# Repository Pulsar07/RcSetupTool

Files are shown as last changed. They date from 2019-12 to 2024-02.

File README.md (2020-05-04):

<div class="PageDoc">

<div class="header">

<div class="headertitle">

<div class="title">

RC-Einstell-Tool Projekt zur Ansteuerung eines Modellflug-Servos und zum
Vermessen von Ruderausschlägen mittels eines Winkelsensors

</div>

</div>

</div>

<div class="contents">

<div class="textblock">

# <span id="intro_sec_de" class="anchor"></span> Übersicht

Das RC Einstell Tool kann eine Servo mittels PWM Pulserzeugung steuern
und die Ansteuerdaten anzeigen. Zusatzlich kann mittels eines
Winkelsensors der Ruderausschlag sehr genau vermessen werden (besser als
0.5mm). Die Benutzeroberfläches ist als Web-Oberfläche ausgelegt, was
eine Bedienung auch mit dem Smartphone zulässt. Eine einfach kleine
Power-Bank dient als Stromversorgung und man kann extrem einfach und
schnell auf der Werkbank beim Bau oder bei Endeinstellarbeiten alle
wichtigen Daten schnell, genau und vollkommen reproduzierbar ablesen.
Hiermit lassen sich Einstellarbeiten auf der Werkbank oder am
aufgebauten Modell sehr professionell, schnell, genau und reproduzierbar
durchführen. Dieses Projekt ist die Zusammenführung von
<https://github.com/Pulsar07/RuderwegMessSensor> und
<https://github.com/Pulsar07/ServoController>
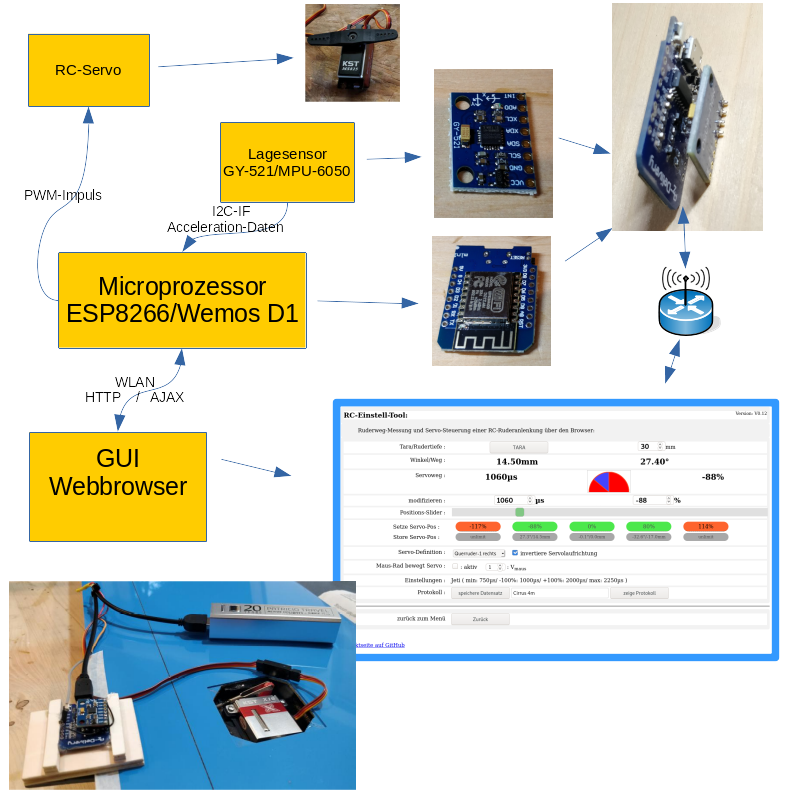
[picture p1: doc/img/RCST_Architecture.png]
Architektur


# <span id="hardware_sec_de" class="anchor"></span> Hardware

## <span id="hardware_subsec_de_mk" class="anchor"></span> Mikrokontroller

Als Mikrokontroller wird der Wemos D1/ESP8266 benutzt, der ausreichende
Rechenpower und Speicherresourcen bietet und eine WLAN Schnittstelle
hat. Es stehen ausgereifte Bibliotheken zur Nutzung der WiFi
Schnittstelle, zur Bereitstellung eines Web-Servers (GUI) und auch zur
Ansteuerung von Servos zur Verfügung.

Hier ein paar Links:

  - <https://www.az-delivery.de/products/d1-mini>
  - <https://github.com/esp8266/Arduino>

## <span id="hardware_subsec_de_ms" class="anchor"></span> Messsensor

Als Messsensor wird der GY-521/MPU-6050 benutzt. Die Genauigkeit liegt
nach Kalibrierung bei Winkeln bis +/- 45° kleiner als 0.5°. Der Baustein
MPU-6050 wird von einer wirklich sehr gut gemachten Libs von J.Rowberg
unterstützt (siehe Link) Der Aufbau sollte auch ohne den Winkelsensor
funktionieren, um nur die Funktion des Servo-Controllers zu erhalten.

Hier ein paar Links:

  - <https://www.invensense.com/wp-content/uploads/2015/02/MPU-6000-Datasheet1.pdf>
  - <https://www.az-delivery.de/products/gy-521-6-achsen-gyroskop-und-beschleunigungssensor>
  - <https://github.com/jrowberg/i2cdevlib/tree/master/Arduino/MPU6050>

## <span id="hardware_subsec_de_sc" class="anchor"></span> Servo-Controller

Für den Servo-Controller ist außer dem Signal-Kabel vom D7-Pin des
Microcontrollers keinerlei Hardware notwendig. Will man nur einen
Winkelmesser bauen, kann dieses Kabel einfach weggelassen werden.

## <span id="hardware_subsec_de_sp" class="anchor"></span> Schaltplan

Der Schaltplan ist denkbar einfach. Es werden nur 4 Verbindungen
zwischen Sensorplatine und Mikrokontroller benötigt. Das Layout und die
Software sind so ausgelegt, dass mit einer Stiftleiste 4x1 das
Sensorboard mit dem Gesicht in Richtung Mikrokontroller direkt verlötet
werden kann.
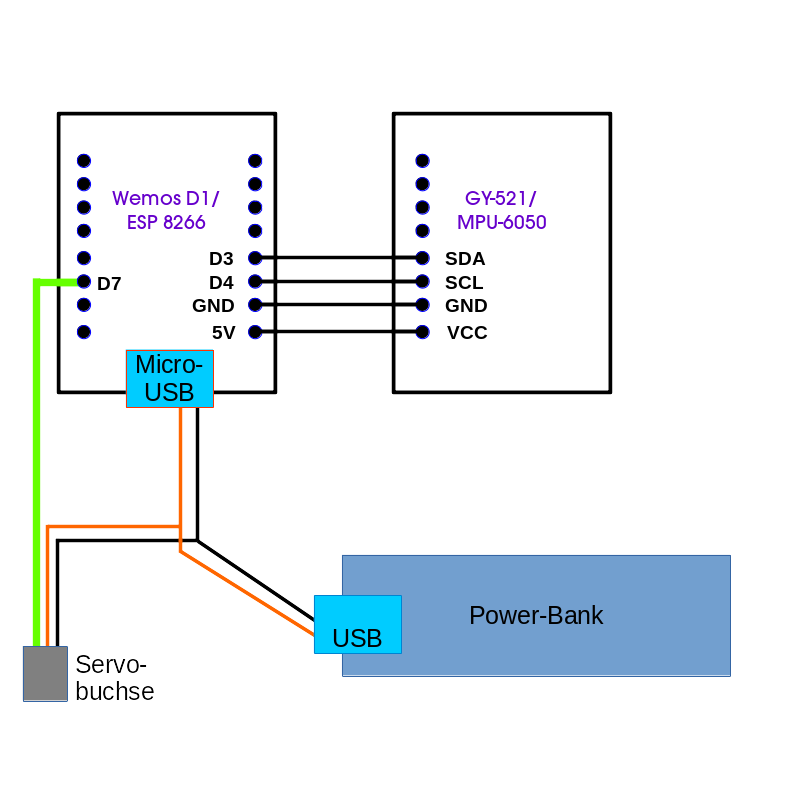
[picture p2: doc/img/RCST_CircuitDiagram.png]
Schaltplan
  
Der Servo wird lediglich mittels eines Signal-Kabels auf den D7 Pin des
Microcontrollers verbunden. Die Plus- und Ground-Verbindung wird mittels
eines auftrennten und wieder zusammengefügten USB-MicroUSB Kabels
hergestellt. Die Servo Stromversorgung wird einfach mittels eines
Servo-Buchsenkabels erstellt und sollte nicht über den Microkontroller
erfolgen, da die Stromstärke zu hoch für diesen ist.

## <span id="hardware_subsec_de_kv" class="anchor"></span> Ruderklemmvorrichtung

Hier kann der geneigte Modellbauer die Kombination aus Microprozessor
und Sensor in eine geeignete Klemmvorrichtung \[ein-\]bauen, die ein
rutschfestes Klemmen am Ruder gewährleistet. So sieht der Prototyp des
Authors aus:
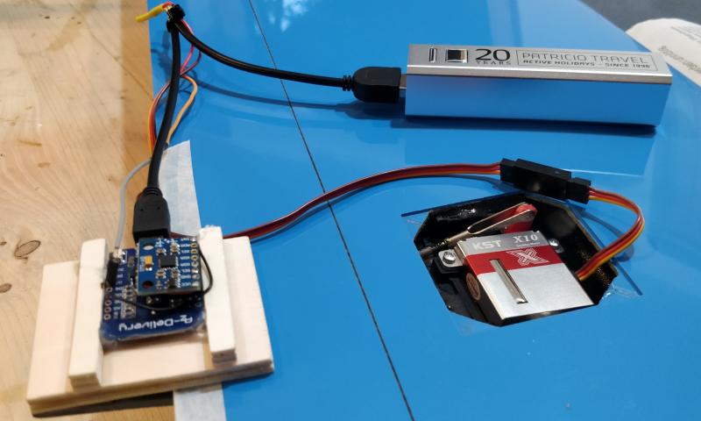
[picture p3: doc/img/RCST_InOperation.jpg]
Klemm


# <span id="hmi_sec_de" class="anchor"></span> Anleitung

## <span id="hmi_subsec_de_ib" class="anchor"></span> Inbetriebnahme

  - Stromversorgung
      - Der Sensor / das Mikroprozessorboard ist mit einem
        Micro-USB-Anschluss ausgestattet, hier kann man jedes
        handelsübliche USB-Netzteil anschließen oder besser jede
        normale Powerbank. Damit ist man in der Werkstatt oder auf dem
        Flugfeld mobil ausgestattet.
  - WiFi
      - Der Sensor muss zuerst mit Smartphone oder PC verbunden werden.
        Dazu stellt der Sensor per WiFi einen Accesspoint mit der SSID
        "UHU" und Kennwort "12345678" zur Verfügung. Ist das Gerät mit
        diesem WLAN verbunden, kann im Web-Browser über die Adresse
        <http://192.168.4.1> die Benutzeroberfläche benutzt und der
        Sensor konfiguriert werden. Sowohl obige SSID als auch das
        Kennwort können danach geändert werden.
      - Auf der Einstellseite kann eine SSID und ein Kennwort für ein
        WLAN (WLAN-Client) konfiguriert werden, mit dem sich der Sensor
        verbinden. Dabei wird dem Sensor eine IP-Adresse zugewiesen, die
        am WLAN-Router abgefragt werden muss. Änderungen der WLAN
        Einstellungen müssen gespeichert werden und werden erst nach
        Neustart aktiv.
      - Ist die Verbindung zu einem WLAN konfiguriert (WLAN-Client),
        kann auf der Einstellungsseite, der Accesspoint deaktiviert
        werden (nach Speichern und Neustart). Kann beim Neustart keine
        Verbindung zum konfigurierten WLAN aufgebaut werden, wird der
        Accesspoint-Mode aber trotzdem aktiviert, damit ein Zugang zum
        Gerät möglich ist.
  - Nutzung des Sensorboard GY-521 mit MPU-6050
      - Genauigkeit: Der MEMS Chip des MPU-6050 sollte Winkelauflösungen
        besser als 0.5° bei 45° Ausschlag messen können, was bei einer
        60mm Rudertiefe von 60mm einen Fehler von kleiner als 0.5mm
        ergibt. Zudem sind diverse Anzeigegenauigkeiten für die Winkel
        und die Ruderwegs-Messung auswählbar. Die Anzeige hat zwar immer
        2 Dezimalstellen, intern wird aber gerundet.
      - Experten-Einstellungen:
          - Kalibrierung: Damit der MPU-6050 allerdings diese
            Genauigkeit erreicht, muss er nachträglich kalibriert
            werden. Die Software unterstützt diese Funktion und kann die
            Werte intern speichern. Zur Kalibrierung muss die
            GY-521-Sensorplatine mit der flachen Rückseite möglichst
            exakt horizontal aufgelegt werden. Dann den Kalibrier-Button
            drücken und ca. 5s warten bis die Kalibrierung beendet ist.
            Dabei sollte die Auflagefläche (Tisch) nicht bewegt werden
            und frei von Vibrationen sein.
          - Einbaulage: Die Sensorplatine sollte auch genau so, wie bei
            der Kalibrierung, betrieben werden. Also die flache Seite
            nach unten und die Seite mit den Elektronikbausteinen nach
            oben. Nur so wird die oben genannte Genauigkeit erreicht.
          - Achsen und Anzeige-Genauigkeit: Auf der Konfigurationsseite,
            kann die Bezugs-Achse der Winkelmessung, je nach Einbaulage
            in der Klemmeinrichtung ausgewählt werden.
          - Kalibrierungsoffset: Hier können Kalibrierungs-Messwerte für
            +/- 45° Referenzmessungen eingebeben werden und
            aktiviert/deaktiviert werden, um die höchst mögliche
            Genauigkeit zu erreichen. Damit werden dann die Messwerte
            auf die Offsetwerte interpoliert. Der Grund hierfür ist, wie
            die Erfahrung zeigt, dass die verfügbaren günstggen
            China-Importe, nicht die höchste Qualität aufweisen. Z.T.
            lassen sich diese Sensoren einfach nicht kalibrieren. Ein
            manuelles Kalibrieren mit diesem Kalibrierungsoffset, bringt
            jedoch meist den gewünschten Erfolg (siehe
            Experten-Einstellungen) und gewährleistet genaues Arbeiten.

## <span id="hmi_subsec_de_me" class="anchor"></span> Winkel-Messung

  - Der mit dem Mikrokontroller verbundene Messensor sollte mit einer
    Klemmvorrichtung fest verbunden sein, und kann dann einfach an eine
    beliebige Stelle des Ruders aufgeklemmt werden. Die Ruderdrehachse,
    sollte möglichst parallel zur ausgewählten Dreh-Achse (X- oder
    Y-Achse) sein. Wie schon beschrieben, muss der Sensor mit dem
    Gesicht nach oben auf dem Ruder befestigt sein.
  - Einschränkungen: Der Sensor kann nur Winkel in Bezug auf die
    Schwerkraft messen. Somit sind Ruderwegsmessungen für das
    Seitenruder nur möglich wenn der Rumpf um 90° gedreht liegt.
  - Der Ruderweg ist abhänig von der Rudertiefe. Diese ist an der Stelle
    zu Messen, an der man den Ruderweg messen will. In der
    Web-Oberfläche des Sensor kann diese Rudertiefe eingegeben werden.
  - Ist der Sensor so auf dem Ruder angebracht, und die Rudertiefe
    eingestellt, ist die Ruderstellung in die Null-Lage zu bringen.
    Jetzt können Winkel und Ruderweg per "Tara"-Button auf 0 gesetzt
    werden.
  - Bewegt man das Ruder nun nach oben oder unten werden die Ausschläge
    in Grad und Millimeter angezeigt. Sollte das Vorzeichen nicht den
    Erwartungen entsprechen, kann dies bei den Einstellungen angepasst
    werden.
  - Zur Flugphasenmessung kann die Min-/Max-Rudermessung benutzt werden.
    Hier sollte man das Ruder in die Neutralstellung der Flugphase
    bringen. Nun den Schalter für die Min-/Max-Ruderweg-Messung
    aktivieren. Damit wird der aktuelle Ruderausschlag als Neutralwert
    übernommen. Jetzt können die beiden Min-/Max-Werte angefahren
    werden. Alle drei Werte werden bis zur Deaktiverung der Messung
    angezeigt.
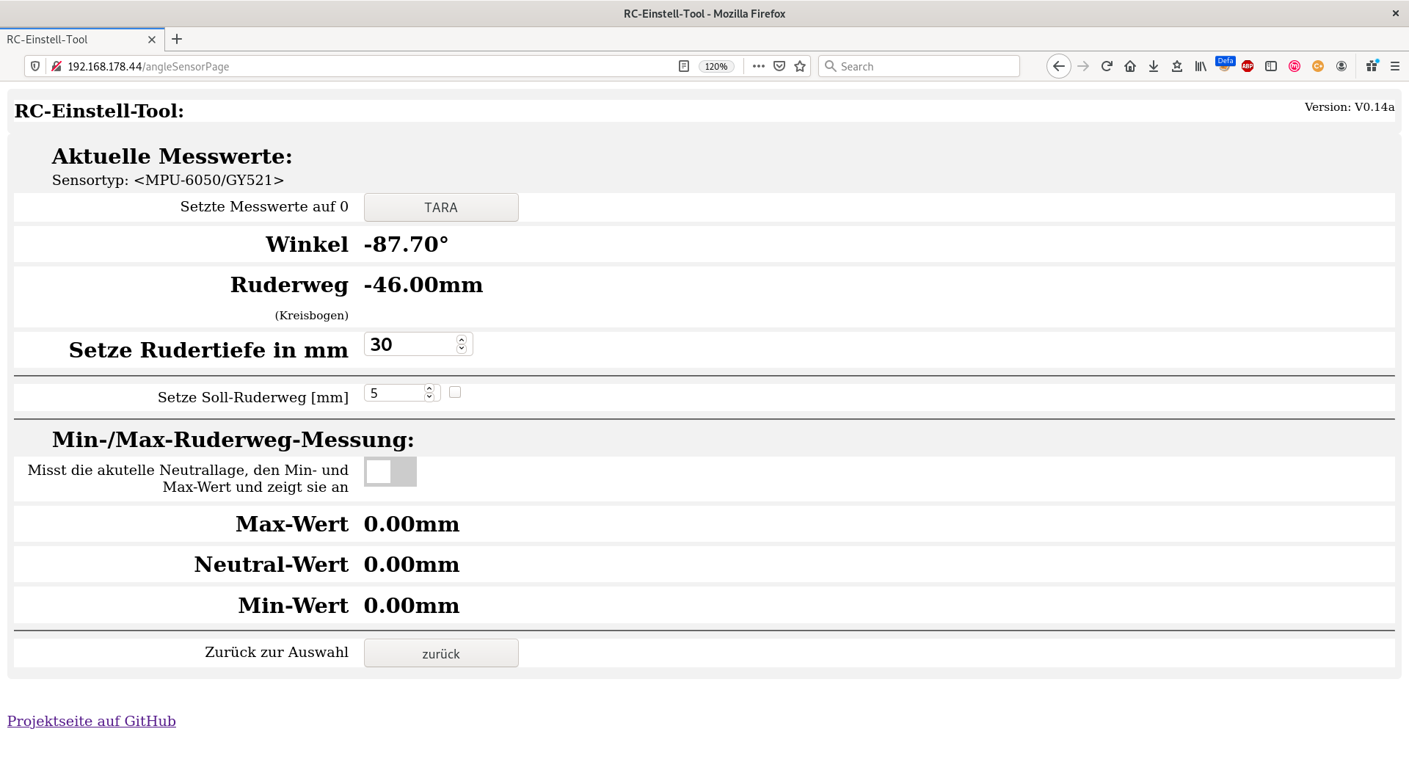
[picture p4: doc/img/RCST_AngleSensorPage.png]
AngleSensorPage
    

## <span id="hmi_subsec_de_sc" class="anchor"></span> Servo-Controller

Die Bedienung am Web-GUI ist denkbar einfach. Die Servo-Position kann
über zwei Eingabefelder prozentual oder als Impulsbreite gesteuert
werden. Zusätzlich kann die Servoposition über ein Slider-Widget
gesteuert werden. Zudem erlaubt eine aktivierbare Maus-Wheel Funktion,
mit Beschleunigungsfaktor, das Steuern des Servowegs mittels der Maus.
Es sind für diverse Aufgaben noch 5 vordefinierte und einstellbare
(Save) Positions-Buttons verfügbar. Die Limit-Buttons, können zum
Begrenzen des Servo-Wegs benutzt werden, um ein versehntliches
Überfahren eines mechanischen Limits zu verhindern. Auf der
Einstellseite, können die Limits und 100%-Settings für verschiedene
Hersteller von RC-Systemen voreingestellt werden, damit die Anzeige
exakt mit den Werte des genutzten RC-System übereinstimmt.
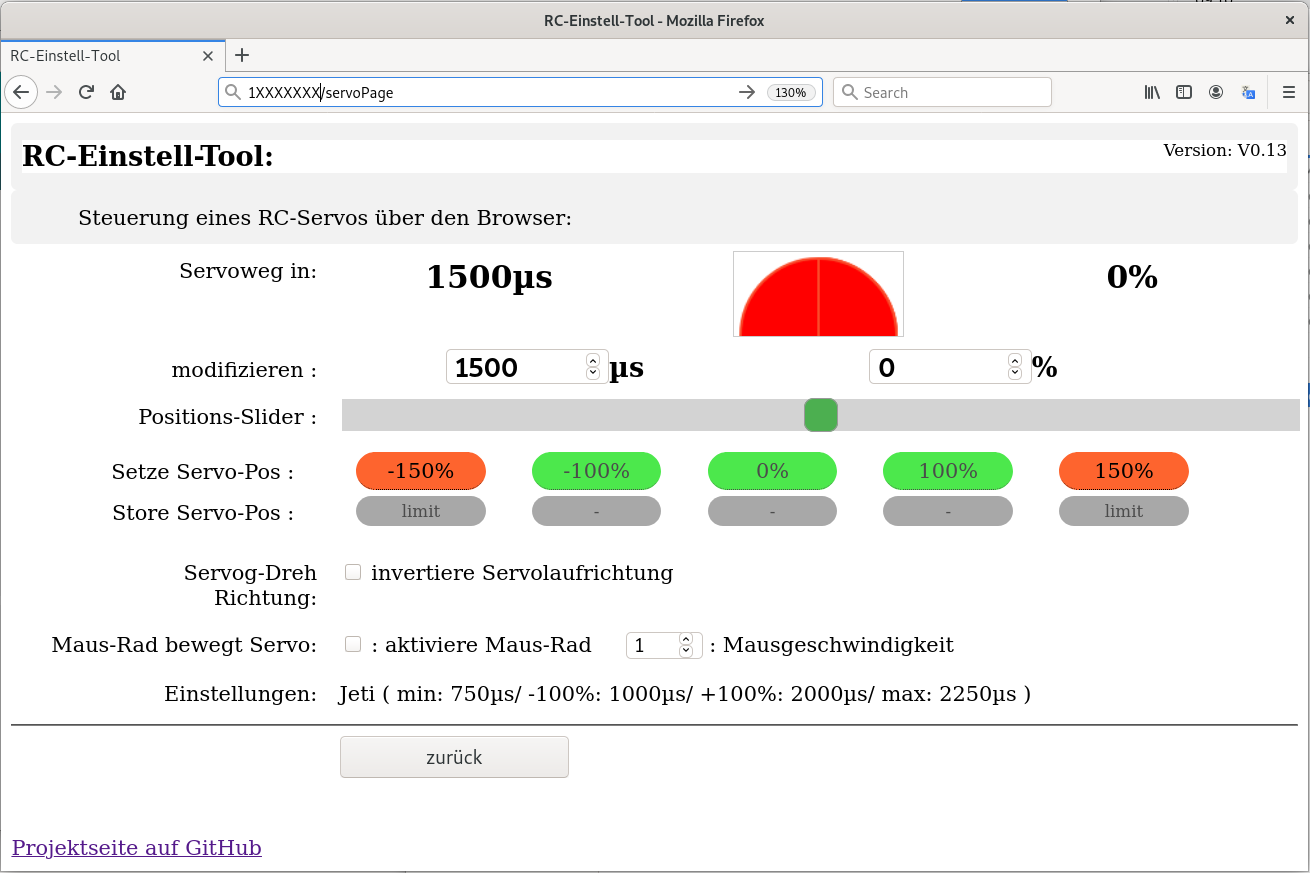
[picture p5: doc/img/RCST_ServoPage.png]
ServoPage


## <span id="hmi_subsec_de_ms" class="anchor"></span> Steuern und Messen

In dieser Ansicht kann sowohl der Servo gesteurt als auch der
Winkel-Sensor abgelesen werden. Dies ist vor allem bei Servo- und
Gestänge-Einbauten ein große Hilfe.
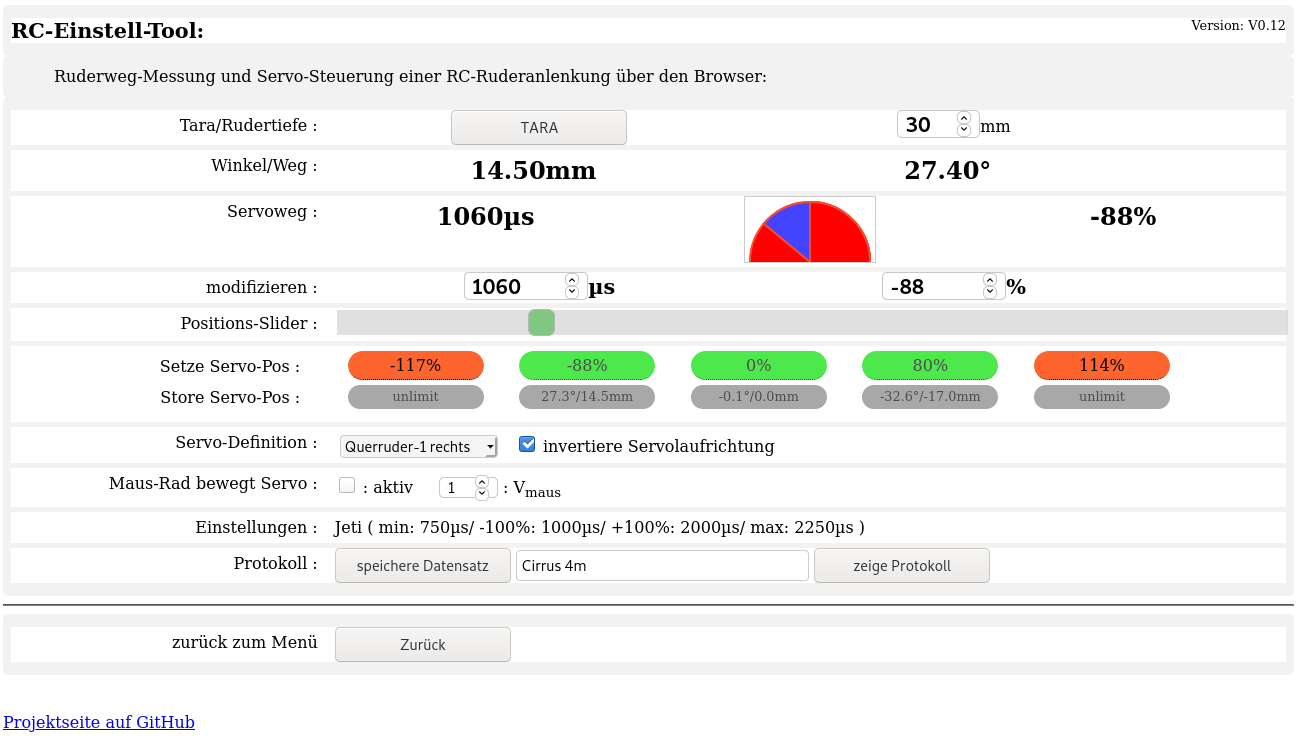
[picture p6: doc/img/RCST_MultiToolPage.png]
MultiToolPage

Zusätzlich können den in den Preset-Buttons gespeicherten Servo-Werte
(und die gemessenen Winkel- und Ruderauschlagswerte) und eine
Nutzer-Beschreibung des Datensatzes festgehalten und mittels der
Funktion "Zeige Protokoll" in Tabellenform ausgegeben werden.
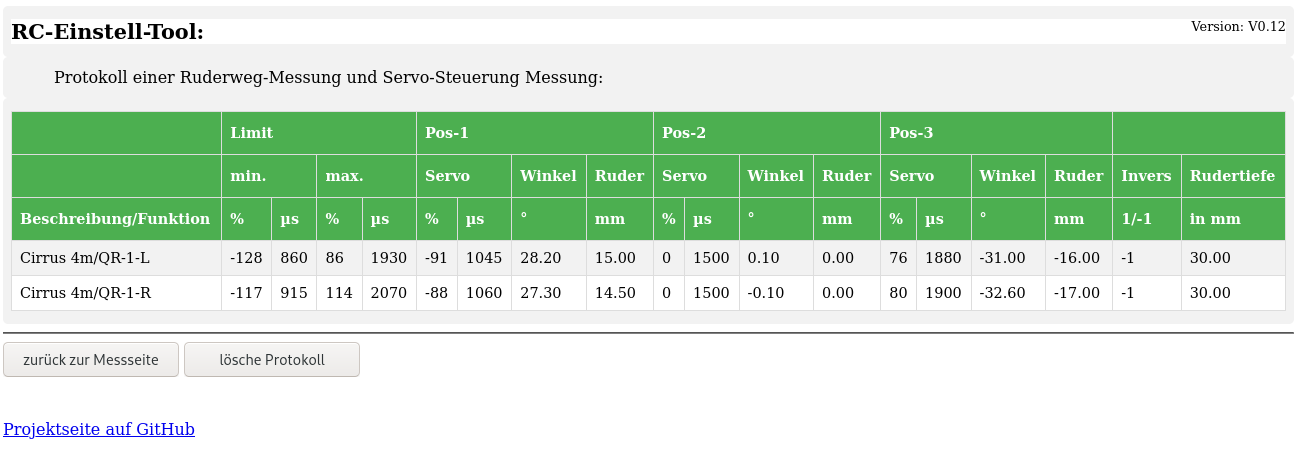
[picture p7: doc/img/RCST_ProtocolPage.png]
ProtocolPage


Weitere Details gibt es unter [Albatross, Seite für Modellflug und
Technik](http://www.so-fa.de/nh/RcSetupTool)

## <span id="hmi_subsec_de_flash" class="anchor"></span> Bin-Datei direkt zum Flashen

ist im bin-Verzeichnis verfügbar. Download NodeMCU-Flasher (z. Bspl. Von
hier:
<https://github.com/marcelstoer/nodemcu-pyflasher/releases/tag/v4.0> )  
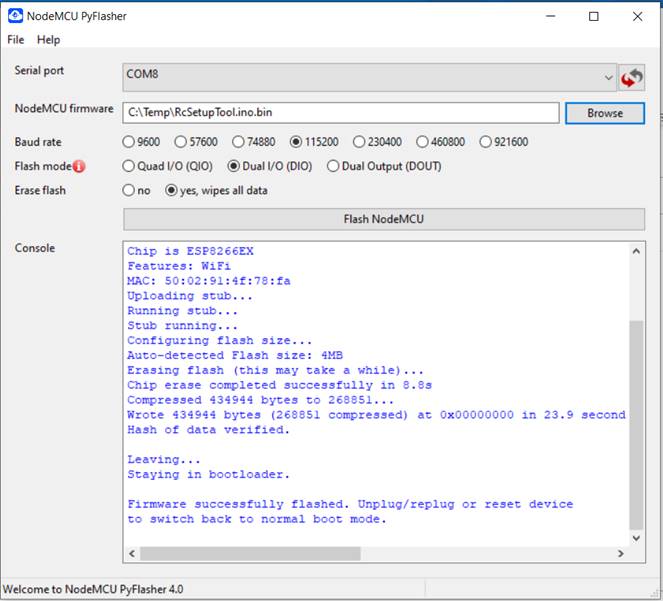
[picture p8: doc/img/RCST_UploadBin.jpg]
UploadBin
  
Flasher-Programm starten und Port wählen, Bin-Datei öffnen und 115200
Baud einstellen.  
Flash-Button drücken.  
Das war es ;-)  

</div>

</div>

</div>

-----

<span class="small">Generated by  
doxygen (http://www.doxygen.org/index.html)
1.8.15</span>

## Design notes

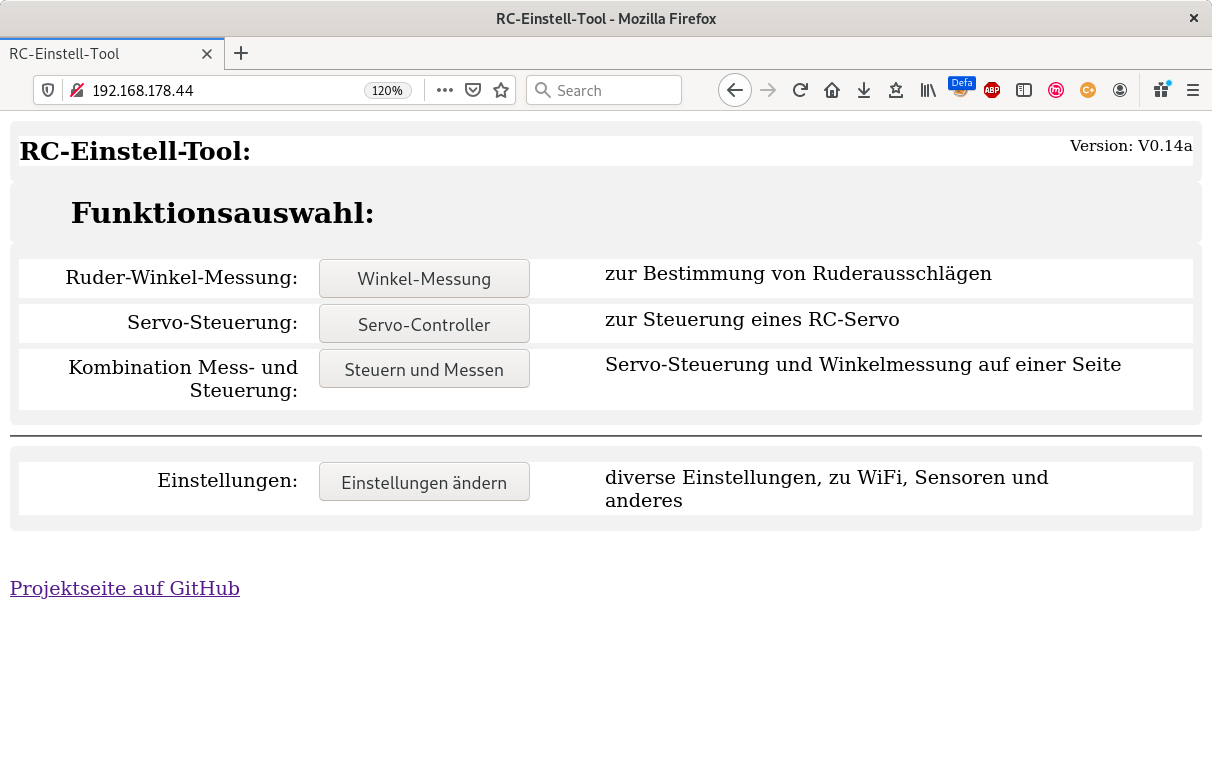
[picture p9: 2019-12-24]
doc/img/RCET_Menu.png

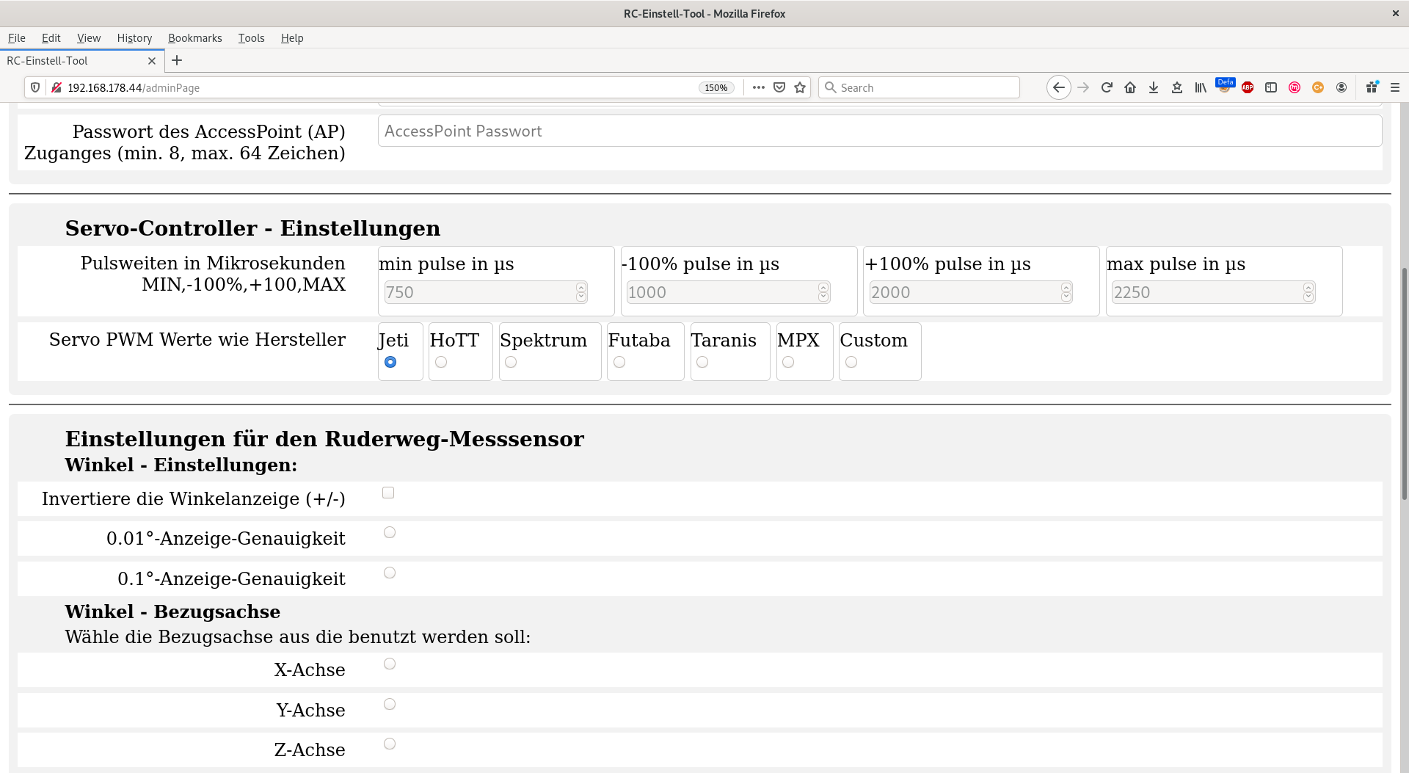
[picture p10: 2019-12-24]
doc/img/RCST_AdminPage.png

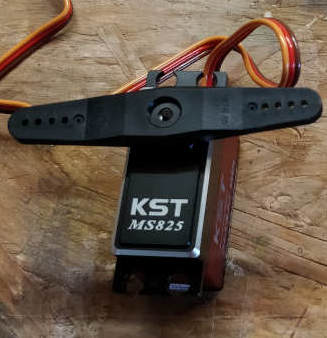
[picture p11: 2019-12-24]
doc/RCServo.jpg

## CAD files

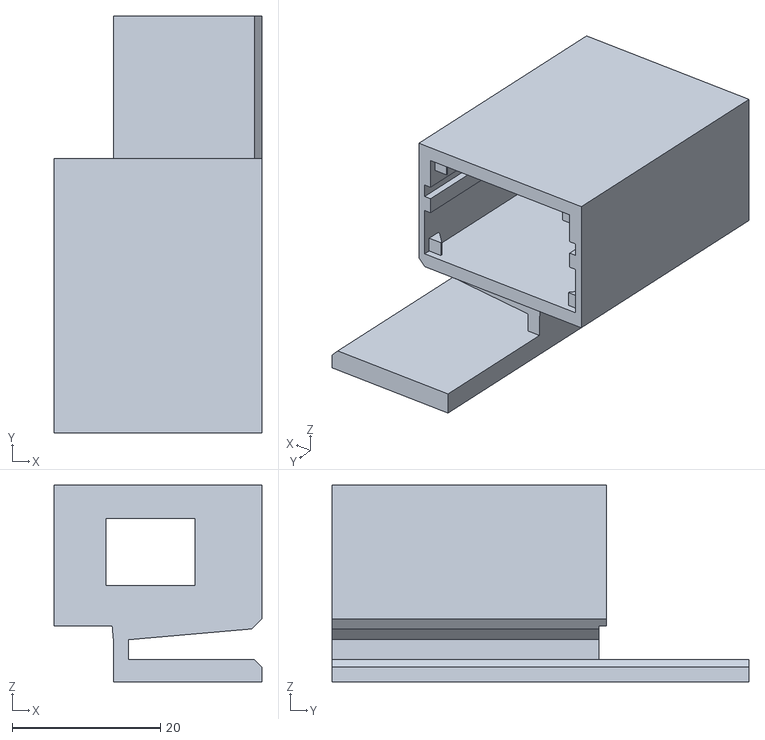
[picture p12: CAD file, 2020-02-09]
box_3d/Gehäuse Winkelmesser 05.stl
28.0 x 56.2 x 26.5

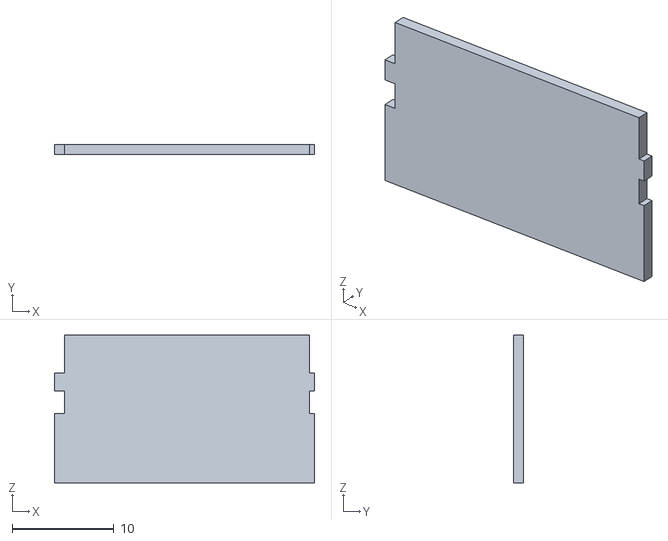
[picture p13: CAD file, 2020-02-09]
box_3d/Deckel.stl
25.5 x 1.00 x 14.5

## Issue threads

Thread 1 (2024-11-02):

V0.175: Build mit Arduino IDE liefert keine Daten an Weboberfläche

vaddl682, 2024-11-02:
Hallo,
ich wollte den aktuellen Stand V0.175 mit der Arduino IDE 2.33 auf den Wemos D1 builden. Die Weboberfläche ist ohne Probleme erreichbar, nur der Sensor liefert keine Daten (blaue LED leuchtet nicht).
Verwende ich die bin Datei und den NodeMCU Flasher funktioniert alles bestens, allerdings ist das noch die alte Version ohne die Verbesserungen. Ein Hardware Fehler ist somit ausgeschlossen.

Können Sie mir weiterhelfen und evtl. die bin Datei auf die aktuelle Version updaten?

Pulsar07, 2024-11-02:
Die Versionen ab V0.17x sind allesamt lediglich Erweiterungen bzgl. einer lokalen Anzeige und Bedienung. Es wird zusätzliche Hardware in Form eines OLED Displays und eines Rotary Encoder Moduls (z.B. KY-040) zur Bedienung benötigt. Ein optionaler Stromsensor und ein Buzzer, misst den Strom zum Servo und kann dann ab einer einstellbaren Schwelle per Buzzer eine Stromwarnung ausgeben.
Die Software in der Version V0.175 ist standardmäßig allen oben genannten Features gebaut. Da das OLED auch über das I2C Interface kommuniziert, dies jedoch bei dir nicht vorhanden ist, kommt es vermutlich zu dem Problem.
Du hast keine Vorteile mit der neuen Version ohne zusätzliche HW. Wenn du dennoch die V0.175 benutzen möchtest, muss du diese defines auskommentieren: ( // )
```
#define WIFI_KIT_8
#define OLED
#define CURRENT_SENSOR
#define ROTARY_ENCODER
```

Habe leider die Beschreibung für die V0.175 noch nicht angepasst, werde es aber die Tage nachholen.

Gruß Rainer

Closed 2025-03-24.

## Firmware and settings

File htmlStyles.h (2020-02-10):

const char STYLES[] PROGMEM = R"=====(
* {
  box-sizing: border-box;
}
canvas {
  border: 1px solid #ccc;
}

h2, h3, h4, p {
  margin: 3px;
  padding: 0px 0px 0px 40px;
}

input[type=text], textarea {
  width: 100%;
  padding: 5px;
  border: 1px solid #ccc;
  border-radius: 4px;
  resize: vertical;
}


input[type=checkbox].config, input[type=radio].config, input[type=number].config, select {
  margin: 5px 12px 5px 5px;
  border: 1px solid #ccc;
  border-radius: 4px;
  display: block;
  display: inline-block;
}

label {
  padding: 6px 12px 6px 0;
  display: block;
  display: inline-block;
}

label.input {
  border: 1px solid #ccc;
  border-radius: 4px;
  display: inline-block;
}

input[type=submit] {
  background-color: #4CAF50;
  color: white;
  padding: 12px 20px;
  border: none;
  border-radius: 4px;
  cursor: pointer;
  float: right;
}

button {
  padding: 3px;
  width: 12em;
}

button:hover {
  background-color: #99f;
}

button.protocol {
  width: 12em;
}

table {
  table-layout: auto;
  border-collapse: collapse;
  font-size: .9em;
  width: 100%;
} 

#protodata td, #protodata th {
  overflow:visible;
  border: 1px solid #ddd;
  padding: 8px;
}

#protodata tr:nth-child(even){background-color: #f2f2f2;}

#protodata tr:hover {background-color: #ddd;}

#protodata th {
  padding-top: 12px;
  padding-bottom: 12px;
  text-align: left;
  background-color: #4CAF50;
  color: white;
}

.container {
  border-radius: 5px;
  background-color: #f2f2f2;
  padding: 8px;
}

.measureRemark {
  font-size: .8em;
}

.measureValue, .flightphaseValue {
  font-size: 1.5em;
  font-weight:bold;
}

.measureInput {
  font-size: 1.3em;
  font-weight:bold;
}

.col-version {
  text-align: right;
  font-size: 0.8em;
  font-weight:normal;
}

.col-appname{
  float: left;
  text-align: left;
  font-size: 1.3em;
  font-weight:bold;
}

.col-declaration, .col-angleView-declaration {
  text-align: right;
  float: left;
  width: 25%;
}

.col-angleView-declaration {
  width: 40%;
}

.col-full, .col-angleView-full{
  text-align: left;
  float: right;
  width: 75%;
  padding-left: 5px;
}

.col-angleView-full{
  width: 55%;
}

.col-full input[type=number] {
  width: 5em;
}

.col-button {
  float: left;
  width: 20%;
  padding: 5px;
}

.col-half {
  text-align: center;
  float: left;
  width: 32.5%;
  padding-left: 5px;
}

.col-third {
  text-align: center;
  float: left;
  width: 25%;
  padding-left: 5px;
}

.col-small {
  text-align: center;
  float: left;
  width: 32.5%;
  padding-left: 5px;
  background-color: #ccc;
}

.col-declaration-long {
  text-align: right;
  float: left;
  width: 25%;
}

.col-declaration-long  input[type=number] {
  width: 3em;
}

.col-button {
  text-align: left;
  float: left;
  width: 20%;
  padding-left: 5px;
}

.col-text {
  text-align: left;
  float: left;
  width: 50%;
  padding-left: 5px;
}

.col-setting-values {
  text-align: left;
  float: right;
  width: 74%;
  padding-left: 5px;
}

.col-setting-descr {
  text-align: right;
  float: left;
  width: 25%;
}

.row {
  background-color: #fff;
  margin: 5px 0px 5px 0px;
}

.row:after {
  content: "";
  display: table;
  clear: both;
}

.c_button_grp, .label_grp {
  display:inline-block;
  padding:0.3em 0.8em;
  margin:0 0.3em 0.3em 0;
}

.c_button_grp {
  width: 17%;
}
a.c_button,a.show_button {
  display:inline-block;
  padding:0.3em 0.8em;
  margin:0 0.3em 0.3em 0;
  width: 100%;
  border-radius:2em;
  box-sizing: border-box;
  text-decoration:none;
  font-weight:500;
  color:#000000;
  background-color: #4CAF50;
  opacity: 0.7;
  -webkit-transition: .2s;
  transition: opacity .2s;
  text-align:center;
  transition: all 0.2s;
}

a.show_button {
  background-color: #666666;
}

a.set_servo {
  background-color: #01DF01;
}

a.store_servo {
  font-size: .8em;
  background-color: #848484;
}

a.c_button:hover {
  opacity: 1;
}

.switch {
 position: relative;
 display: inline-block;
 width: 60px;
 height: 34px;
}

/* Hide default HTML checkbox */
.switch input {
 opacity: 0;
 width: 0;
 height: 0;
}

/* The slidebox */
.slidebox {
 position: absolute;
 cursor: pointer;
 top: 0;
 left: 0;
 right: 0;
 bottom: 0;
 background-color: #ccc;
 -webkit-transition: .4s;
 transition: .4s;
}

.slidebox:before {
 position: absolute;
 content: "";
 height: 26px;
 width: 26px;
 left: 4px;
 bottom: 4px;
 background-color: white;
 -webkit-transition: .4s;
 transition: .4s;
}

input:checked + .slidebox {
 background-color: #2196F3;
}

input:focus + .slidebox {
 box-shadow: 0 0 1px #2196F3;
}

input:checked + .slidebox:before {
 -webkit-transform: translateX(26px);
 -ms-transform: translateX(26px);
 transform: translateX(26px);
}

/* Rounded slidebox */
.slidebox.round {
 border-radius: 34px;
}

.slidebox.round:before {
 border-radius: 50%;
}

.slider {
  -webkit-appearance: none;
  width: 100%;
  height: 25px;
  background: #d3d3d3;
  outline: none;
  opacity: 0.7;
  -webkit-transition: .2s;
  transition: opacity .2s;
}

.slider:hover {
  opacity: 1;
}

.slider::-webkit-slider-thumb {
  -webkit-appearance: none;
  appearance: none;
  width: 25px;
  height: 25px;
  background: #4CAF50;
  cursor: pointer;
}

.slider::-moz-range-thumb {
  width: 25px;
  height: 25px;
  background: #4CAF50;
  cursor: pointer;
}

a.limiter {
  background-color: #FE642E;
  opacity: 1.0;
}

.tooltip {
  position: relative;
  display: inline-block;
  border-bottom: 1px dotted black;
}
.tooltip .tooltiptext {
  visibility: hidden;
  width: 120px;
  background-color: black;
  color: #fff;
  text-align: center;
  border-radius: 6px;
  padding: 5px 0;
  position: absolute;
  z-index: 1;
  top: -5px;
  right: 110%;
}

.tooltip .tooltiptext::after {
  content: "";
  position: absolute;
  top: 50%;
  left: 100%;
  margin-top: -5px;
  border-width: 5px;
  border-style: solid;
  border-color: transparent transparent transparent black;
}
.tooltip:hover .tooltiptext {
  visibility: visible;
  opacity: 0.7;
}

 /* Dropdown Button */
.dropbtn {
  background-color: #4CAF50;
  color: white;
  padding: 16px;
  font-size: 16px;
  border: none;
}

/* The container <div> - needed to position the dropdown content */
.dropdown {
  position: relative;
  position: absolute;
  display: inline-block;
}

/* Dropdown Content (Hidden by Default) */
.dropdown-content {
  display: none;
  position: absolute;
  background-color: #f1f1f1;
  min-width: 160px;
  box-shadow: 0px 8px 16px 0px rgba(0,0,0,0.2);
  z-index: 1;
}

/* Links inside the dropdown */
.dropdown-content a {
  color: black;
  padding: 12px 16px;
  text-decoration: none;
  display: block;
}

/* Change color of dropdown links on hover */
.dropdown-content a:hover {background-color: #ddd;}

/* Show the dropdown menu on hover */
.dropdown:hover .dropdown-content {display: block;}
.dropdown-rs:hover .dropdown-content {display: block;}
.dropdown-rs:hover .dropdown-touch {display: block;}
.dropdown-rs:hover:active {display: none;}
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

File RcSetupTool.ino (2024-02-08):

#include <EEPROM.h>
#include <ESP8266WiFi.h>
#include <ESP8266WebServer.h>
// #define DEBUG_ESP_MDNS

#include <ESP8266mDNS.h>
#include <DNSServer.h>
#include <Servo.h>

// *** CONFIGURAITON ***
// Used Ports as as summary (WiFi-Kit-8)
/*
D0 : OLED Reset
D1 : I2C-SCL OLED + GY521
D2 : I2C-SDA OLED + GY521
D3 : Drehwinkelgeber CLK
D4 : free
D5 : ServoOut
D6 : Drehwinkelgeber PushButton
D7 : Drehwinkelgeber DT
D8 : Buzzer
D9 : TX
D10: RX
*/

#define WIFI_KIT_8 
#define OLED
#define CURRENT_SENSOR
#define ROTARY_ENCODER
#define SERVO_PIN D5
#define PIN_BUZZER_OUT D8
#define PIN_PUSH_BUTTON D6

// **** Voltage measurement settings ****

// analog input pin
#define VOLTAGE_PIN                   A0

// supply voltage

static const char myName[] = "RcSetupTool";
long ourDebug1;
long ourDebug2;
String ourDebug3;



#ifdef OLED
#include <U8g2lib.h>        // Universal 8bit Graphics Library (https://github.com/olikraus/u8g2/)

#ifdef WIFI_KIT_8 
  // Wifi Kit 8 has a fixed wired 128x32 display 
  // U8G2_SSD1306_128X32_UNIVISION_1_HW_I2C ourOLED(U8G2_R0, /* reset=*/ 16, /* clock=*/ 5, /* data=*/ 4); 
  U8G2_SSD1306_128X32_UNIVISION_1_HW_I2C ourOLED(U8G2_R0, /* reset=*/ D0, /* clock=*/ D1, /* data=*/ D2); 
#else 
  U8G2_SH1106_128X64_NONAME_1_HW_I2C ourOLED(U8G2_R0, /* reset=*/ U8X8_PIN_NONE, /* clock=*/ D3, /* data=*/ D4); 
  //U8G2_SSD1306_128X64_NONAME_1_HW_I2C ourOLED(U8G2_R0, /* reset=*/ U8X8_PIN_NONE, /* clock=*/ D3, /* data=*/ D4); 
#endif 
#endif

#ifdef ROTARY_ENCODER
#include <Encoder.h>
Encoder ourRotaryEncoder(D7, D3);
#define RE_MULITPLIER_SLOW 1
#define RE_MULITPLIER_NORMAL 5
long ourRotaryEncoderPosition=0;
long ourRotaryMenuPosition=0;
uint8_t ourRotaryEncoderMultiplier;
static boolean ourREState = true;
static int8_t ourREInversion = 1; 
static long ourREPos = 0;
static long ourREOldPos  = 0;

#include <Bounce2.h>
Bounce2::Button ourPushButton = Bounce2::Button();
#endif

#define OTA
#ifdef OTA
#include <ArduinoOTA.h>
#endif


#include "htmlAdminPage.h"
#include "htmlExpertPage.h"
#include "htmlMenuPage.h"
#include "htmlServoPage.h"
#include "htmlAngleSensorPage.h"
#include "htmlMultiToolPage.h"
#include "htmlShowProtocolTablePage.h"
#include "htmlScript.h"
#include "htmlStyles.h"
#include "Config.h"


// !!!!!!!!!!!!!!!!!!
// if you enable this define, the sligthly patched lib
// Adafruit_MMA8451_Library from 
// https://github.com/Pulsar07/Adafruit_MMA8451_Library
// has to be added to the arduino library folder
// #define SUPPORT_MMA8451
// !!!!!!!!!!!!!!!!!!
#ifdef SUPPORT_MMA8451
#include <Adafruit_MMA8451.h>         // MMA8451 library
#endif
// I2Cdev and MPU6050 must be installed as libraries, or else the .cpp/.h files
// for both classes must be in the include path of your project
#include "I2Cdev.h"
// #define USE_MPU6050_MPU
#ifdef USE_MPU6050_MPU
#include "MPU6050_6Axis_MotionApps20.h"
#else
#include "MPU6050.h"
#endif

// #define DO_LOG

// Version history
// V0.10 : full functional initial version
//         merge of ServoController and RuderwegMesssensor
// V0.11 : protocol page to multiToolPage added and some bug fixes
// V0.12 : some small beautifications
// V0.13 : support for all ASCII special chars in SSID and passwords
//         more enhanced preset and protocol behaviour
// V0.14 : provided patched Adafruit_MMA8451_Library in the repository
// V0.15 : fixed support for USE_MPU6050_MPU
// V0.16 : fixed layout problems in angle measure view and bug in audio context for reference value handling
// V0.161 : fixed CTRL-Key handling for Macs
// V0.162 : expert menu now as a separate button, and AJAX get requets will work with ESP32 web server
// V0.170 : first draft: support for working OLED GUI for servo page, angle page and settings for angle tara, rudder depth, servo steps and servo null value
// V0.171 : second draft: more menus and settings an enhance GUI vor the 128x32 OLED
// V0.172 : bug fix: current smoothing disabled, menu back handling with one click fixed
// V0.173 : bug fix: current / ACS712 handling optimized and some other small enhancements
// V0.174 : new settings for buzzer, angle and rudder inversion, display rotation and safe config
// V0.175 : new settings for max current alarm and some menu enhancements

#define APP_VERSION "V0.175"

/**
 * \file RcSetupTool.ino
 *
 * \brief small tool to control an rc-servo and measure the rudder throw via a web browser
 *
 * \author Author: Rainer Stransky
 *
 * \copyright This project is released under the GNU Public License v3
 *          see https://www.gnu.org/licenses/gpl.html.
 * Contact: opensource@so-fa.de
 *
 */

/**
 * \mainpage RC-Einstell-Tool Projekt zur Ansteuerung eines Modellflug-Servos und zum Vermessen von Ruderausschlägen mittels eines Winkelsensors
 *
 * \section intro_sec_de Übersicht
 * Das RC Einstell Tool kann eine Servo mittels PWM Pulserzeugung steuern und die Ansteuerdaten anzeigen.
 * Zusatzlich kann mittels eines Winkelsensors der Ruderausschlag sehr genau vermessen werden (besser als 0.5mm).
 * Die Benutzeroberfläches ist als Web-Oberfläche ausgelegt, was eine Bedienung auch mit dem Smartphone zulässt.
 * Eine einfach kleine Power-Bank dient als Stromversorgung und man kann extrem einfach und schnell auf der Werkbank beim
 * Bau oder bei Endeinstellarbeiten alle wichtigen Daten schnell, genau und vollkommen reproduzierbar ablesen.
 * Hiermit lassen sich Einstellarbeiten auf der Werkbank oder am aufgebauten Modell sehr professionell, schnell,
 * genau und reproduzierbar durchführen.
 * Dieses Projekt ist die Zusammenführung von https://github.com/Pulsar07/RuderwegMessSensor und https://github.com/Pulsar07/ServoController
 * ![Architektur](https://raw.githubusercontent.com/Pulsar07/RcSetupTool/master/doc/img/RCST_Architecture.png)
 *
 * \section hardware_sec_de Hardware
 * \subsection hardware_subsec_de_mk Mikrokontroller
 * Als Mikrokontroller wird der Wemos D1/ESP8266 benutzt, der ausreichende Rechenpower und
 * Speicherresourcen bietet und eine WLAN Schnittstelle hat. Es stehen ausgereifte Bibliotheken zur Nutzung der WiFi
 * Schnittstelle, zur Bereitstellung eines Web-Servers (GUI) und auch zur Ansteuerung von Servos zur Verfügung.
 *
 * Hier ein paar Links:
 * * https://www.az-delivery.de/products/d1-mini
 * * https://github.com/esp8266/Arduino
 *
 * \subsection hardware_subsec_de_ms Messsensor
 * Als Messsensor wird der GY-521/MPU-6050 benutzt. Die Genauigkeit liegt nach Kalibrierung bei
 * Winkeln bis +/- 45° kleiner als 0.5°. Der Baustein MPU-6050 wird von einer wirklich sehr gut
 * gemachten Libs von J.Rowberg unterstützt (siehe Link)
 * Der Aufbau sollte auch ohne den Winkelsensor funktionieren, um nur die Funktion des Servo-Controllers zu erhalten.
 *
 * Hier ein paar Links:
 * * https://www.invensense.com/wp-content/uploads/2015/02/MPU-6000-Datasheet1.pdf
 * * https://www.az-delivery.de/products/gy-521-6-achsen-gyroskop-und-beschleunigungssensor
 * * https://github.com/jrowberg/i2cdevlib/tree/master/Arduino/MPU6050
 *
 * \subsection hardware_subsec_de_sc Servo-Controller
 * Für den Servo-Controller ist außer dem Signal-Kabel vom D7-Pin des Microcontrollers keinerlei Hardware notwendig.
 * Will man nur einen Winkelmesser bauen, kann dieses Kabel einfach weggelassen werden.
 *
 * \subsection hardware_subsec_de_sp Schaltplan
 * Der Schaltplan ist denkbar einfach. Es werden nur 4 Verbindungen zwischen Sensorplatine und
 * Mikrokontroller benötigt. Das Layout und die Software sind so ausgelegt, dass mit einer Stiftleiste
 * 4x1 das Sensorboard mit dem Gesicht in Richtung Mikrokontroller direkt verlötet werden kann.
 * ![Schaltplan](https://raw.githubusercontent.com/Pulsar07/RcSetupTool/master/doc/img/RCST_CircuitDiagram.png)
 * <br>Der Servo wird lediglich mittels eines Signal-Kabels auf den D7 Pin des Microcontrollers verbunden.
 * Die Plus- und Ground-Verbindung wird mittels eines auftrennten und wieder zusammengefügten USB-MicroUSB Kabels
 * hergestellt. Die Servo Stromversorgung wird einfach mittels eines Servo-Buchsenkabels erstellt und
 * sollte nicht über den Microkontroller erfolgen, da die Stromstärke zu hoch für
 * diesen ist.
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
void loop()
{
  static unsigned long last = 0;
  unsigned long now = millis();
  server.handleClient();
  ourDNSServer.processNextRequest();
  MDNS.update();

  moveServo();
  readMotionSensor();
  #ifdef ROTARY_ENCODER
  updateRotaryEncoder(now);
  updatePushButton(now);
  #endif
  #ifdef OLED
  updateOLED(now);
  #endif
  updateBuzzer(now);
  #ifdef CURRENT_SENSOR
  updateCurrentSensor(now);
  #endif

  doAsync();

  if (WiFi.status() == WL_CONNECTED) {
    #ifdef OTA
    ArduinoOTA.handle();
    #endif
  }


  if ( (millis() - last) > 500) {
    // showServoPos();
    prepareMotionData();
    last = millis();
  }
}


// OVER THE AIR
#ifdef OTA
void setup_ota() {
  // Port defaults to 8266
  // ArduinoOTA.setPort(8266);

  // Hostname defaults to esp8266-[ChipID]
  // ArduinoOTA.setHostname(String("esp8266" + WiFi.macAddress()).c_str());

  // No authentication by default
  ArduinoOTA.setPassword("admin");

  // Password can be set with it's md5 value as well
  // MD5(admin) = 21232f297a57a5a743894a0e4a801fc3
  // ArduinoOTA.setPasswordHash("21232f297a57a5a743894a0e4a801fc3");

  ArduinoOTA.onStart([]() {
    String type;
    if (ArduinoOTA.getCommand() == U_FLASH) {
      type = F("sketch");
    } else { // U_FS
      type = F("filesystem");
    }

    // NOTE: if updating FS this would be the place to unmount FS using FS.end()
    Serial.println(F("Start updating ") + type);
  });
  ArduinoOTA.onEnd([]() {
    Serial.println(F("\nEnd"));
  });
  ArduinoOTA.onProgress([](unsigned int progress, unsigned int total) {
    Serial.printf("Progress: %u%%\r", (progress / (total / 100)));
  });
  ArduinoOTA.onError([](ota_error_t error) {
    Serial.printf("Error[%u]: ", error);
    if (error == OTA_AUTH_ERROR) {
      Serial.println(F("Auth Failed"));
    } else if (error == OTA_BEGIN_ERROR) {
      Serial.println(F("Begin Failed"));
    } else if (error == OTA_CONNECT_ERROR) {
      Serial.println(F("Connect Failed"));
    } else if (error == OTA_RECEIVE_ERROR) {
      Serial.println(F("Receive Failed"));
    } else if (error == OTA_END_ERROR) {
      Serial.println(F("End Failed"));
    }
  });
  ArduinoOTA.begin();
  Serial.print(F("ArduinoOTA: setup ready"));
  Serial.print(F("  IP address: "));
  Serial.println(WiFi.localIP());
}
#endif
// End: OVER THE AIR


// =================================
// sensor data processing functions
// =================================

void initConfig() {
  initServoControllerConfig();
  initAngleMeasure();
}

void initAngleMeasure() {
  // if EEPROM config was not properly stored
  if (ourConfig.amplitudeInversion != -1) {
    ourConfig.amplitudeInversion = 1;
  }
  if (ourConfig.angleInversion != -1) {
    ourConfig.angleInversion = 1;
  }
  if (ourConfig.rudderSize < 0 || ourConfig.rudderSize > 300) {
    ourConfig.rudderSize = 30;
  }
  if (String((uint8_t) ourConfig.calibrationOffsetEnabled).equals("255")) {
    // if config is not stored before
    ourConfig.calibrationOffsetEnabled = false;
    ourConfig.calibrationOffsetHigh = 450;
    ourConfig.calibrationOffsetLow = -450;
  }
}


/**
  set the value of the preset store given by aNum in percent
*/
void initPresetInPercent(uint8_t aNum, uint16_t aPercent) {
  if (aNum < CONFIG_SERVO_PRESET_MAX) {
    ourConfig.servoPresets[aNum] = convertPercent2MicroSeconds(aPercent);
    ourProtocolData.currentPresetAngles[aNum] = ANGLE_UNSET_VAL;
  }
}

void initServoControllerConfig() {

  if (ourConfig.servoRangeByVendor < 0 || ourConfig.servoRangeByVendor > custom) {
    ourConfig.servoRangeByVendor = jeti;
  }
  initServoRangeSettings(ourConfig.servoRangeByVendor);
  for (int i=0; i<CONFIG_SERVO_PRESET_MAX; i++) {
    initPresetInPercent(i, (-100 + i*100));
  }
}

void initProtocolData() {
  for (int i=0; i<CONFIG_SERVO_PRESET_MAX; i++) {
    ourProtocolData.currentPresetAngles[i] = ANGLE_UNSET_VAL;
  }
}

void initServo() {
  Serial.print("Servo connected to: ");
  Serial.println(SERVO_PIN);
  ourServo.attach(SERVO_PIN,
    ourConfig.servoPulseWidthPairFullRange[MIN_IDX],
    ourConfig.servoPulseWidthPairFullRange[MAX_IDX]);
  setServoPosInMicroSeconds((ourConfig.servoPulseWidthPairFullRange[MIN_IDX] +
     ourConfig.servoPulseWidthPairFullRange[MAX_IDX]) /2);
  ourServo.writeMicroseconds(getServoPosInMicroSeconds());

  // check and reset servo preset values if not valid initialized
  for (int i=0; i<CONFIG_SERVO_PRESET_MAX; i++) {
    if (getPreset(i) < -125 || getPreset(i) > +125) {
      initPresetInPercent(i, (-100 + i*100));
    }
  }
}

void initServoRangeSettings(rc_vendor_t aVendor) {
  switch (aVendor) {
  case jeti:
    ourConfig.servoPulseWidthPairFullRange[MIN_IDX] = 750;
    ourConfig.servoPulseWidthPairFullRange[MAX_IDX] = 2250;
    ourConfig.servoPulseWidthPair100Percent[MIN_IDX] = 1000;
    ourConfig.servoPulseWidthPair100Percent[MAX_IDX] = 2000;
    break;
  case futaba:
    ourConfig.servoPulseWidthPairFullRange[MIN_IDX] = 920;
    ourConfig.servoPulseWidthPairFullRange[MAX_IDX] = 2150;
    ourConfig.servoPulseWidthPair100Percent[MIN_IDX] = 960;
    ourConfig.servoPulseWidthPair100Percent[MAX_IDX] = 2080;
    break;
  case hott:
  case spektrum:
    ourConfig.servoPulseWidthPairFullRange[MIN_IDX] = 900;
    ourConfig.servoPulseWidthPairFullRange[MAX_IDX] = 2100;
    ourConfig.servoPulseWidthPair100Percent[MIN_IDX] = 1100;
    ourConfig.servoPulseWidthPair100Percent[MAX_IDX] = 1900;
    break;
  case taranis:
    ourConfig.servoPulseWidthPairFullRange[MIN_IDX] = 732;
    ourConfig.servoPulseWidthPairFullRange[MAX_IDX] = 2268;
    ourConfig.servoPulseWidthPair100Percent[MIN_IDX] = 988;
    ourConfig.servoPulseWidthPair100Percent[MAX_IDX] = 2012;
    break;
  case multiplex:
    ourConfig.servoPulseWidthPairFullRange[MIN_IDX] = 750;
    ourConfig.servoPulseWidthPairFullRange[MAX_IDX] = 2250;
    ourConfig.servoPulseWidthPair100Percent[MIN_IDX] = 950;
    ourConfig.servoPulseWidthPair100Percent[MAX_IDX] = 2050;
    break;
  default: // custom
    break;
  }
  ourServoLimit[MIN_IDX] = ourConfig.servoPulseWidthPairFullRange[MIN_IDX];
  ourServoLimit[MAX_IDX] = ourConfig.servoPulseWidthPairFullRange[MAX_IDX];
  printServoRanges();
}

void printServoRanges() {
  Serial.print("FullRange[MIN_IDX]"); Serial.println(ourConfig.servoPulseWidthPairFullRange[MIN_IDX]);
  Serial.print("FullRange[MAX_IDX]"); Serial.println(ourConfig.servoPulseWidthPairFullRange[MAX_IDX]);
  Serial.print("100Percent[MAX_IDX]"); Serial.println(ourConfig.servoPulseWidthPair100Percent[MIN_IDX]);
  Serial.print("100Percent[CFG_MIN]"); Serial.println(ourConfig.servoPulseWidthPair100Percent[MAX_IDX]);
}

void readMotionSensor() {
  if (isI2C_MPU6050Addr()) {
    mpu.getMotion6(&ourAccelerometer_x, &ourAccelerometer_y, &ourAccelerometer_z, &gyro_x, &gyro_y, &gyro_z);
  }
#ifdef SUPPORT_MMA8451
  else if (isI2C_MMA8451Addr()) {
    mma.read();
    ourAccelerometer_x = mma.x;
    ourAccelerometer_y = mma.y;
    ourAccelerometer_z = mma.z;
  }
#endif

  const static double smooth = 0.98d;
  // print out data
  ourSmoothedAngle_x = irr_low_pass_filter(ourSmoothedAngle_x,
    atan2(ourAccelerometer_y, ourAccelerometer_z) * 180 / M_PI, smooth);
  ourSmoothedAngle_y = irr_low_pass_filter(ourSmoothedAngle_y,
    atan2(ourAccelerometer_z, ourAccelerometer_x) * 180 / M_PI, smooth);
  ourSmoothedAngle_z = irr_low_pass_filter(ourSmoothedAngle_z,
    atan2(ourAccelerometer_x, ourAccelerometer_y) * 180 / M_PI, smooth);
  ourSmoothedGyro_x = irr_low_pass_filter(ourSmoothedGyro_x, gyro_x, smooth);
  ourSmoothedGyro_y = irr_low_pass_filter(ourSmoothedGyro_y, gyro_y, smooth);
  ourSmoothedGyro_z = irr_low_pass_filter(ourSmoothedGyro_z, gyro_z, smooth);
}

void prepareMotionData() {
  double effAngle_x = ourSmoothedAngle_x - ourTaraAngle_x;
  double effAngle_y = ourSmoothedAngle_y - ourTaraAngle_y;
  double effAngle_z = ourSmoothedAngle_z - ourTaraAngle_z;
  double effGyro_x = ourSmoothedGyro_x - ourTaraGyro_x;
  double effGyro_y = ourSmoothedGyro_y - ourTaraGyro_y;
  double effGyro_z = ourSmoothedGyro_z - ourTaraGyro_z;
  // Serial.print(String("WX = ") + roundToDot5(effAngle_x));
  // Serial.print(String(" WY = ") + roundToDot5(effAngle_y));
  // Serial.print(String(" WZ = ") + roundToDot5(effAngle_z));
  // Serial.print(String(" GX = ") + roundToDot5(effGyro_x));
  // Serial.print(String(" GY = ") + roundToDot5(effGyro_y));
  // Serial.print(String(" GZ = ") + roundToDot5(effGyro_z));
  // Serial.println();
}
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

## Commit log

2019-12-24 V0.10 : full functional initial version - merge of ServoController and RuderwegMesssensor
2019-12-27 V0.11 : protocol page to multiToolPage added and some bug fixes
    [RcSetupTool.ino]
2020-02-05 Add files via upload
    enclosure stl-files for 3d-printing
    [Deckel.stl, Gehäuse Winkelmesser 05.stl]
2020-02-09 V0.15 : fixed support for USE_MPU6050_MPU
    [RcSetupTool.ino]
2020-02-10 V0.16 : fixed layout problems in angle measure view and bug in audio context for reference value handling
    [Deckel.stl, Gehäuse Winkelmesser 05.stl]
2020-05-01 V0.161 : fixed CTRL-Key handling for Macs
    [RcSetupTool.ino]
2020-05-04 V0.162 : expert menu now as a separate button, and AJAX get requets will work with ESP32 web server
2024-01-25 V0.170 : first draft: support for working OLED GUI for servo page, angle page and settings for angle tara, rudder depth, servo steps and servo null value
2024-01-27 V0.172 : bug fix: current smoothing disabled, menu back handling with one click fixed
    [RcSetupTool.ino]
2024-01-28 V0.173 : bug fix: current / ACS712 handling optimized and some other small enhancements
    [RcSetupTool.ino]
2024-01-31 V0.174 : new settings for buzzer, angle and rudder inversion, display rotation and safe config
    [RcSetupTool.ino]
2024-02-08 V0.175 : new settings for max current alarm and some menu enhancements
